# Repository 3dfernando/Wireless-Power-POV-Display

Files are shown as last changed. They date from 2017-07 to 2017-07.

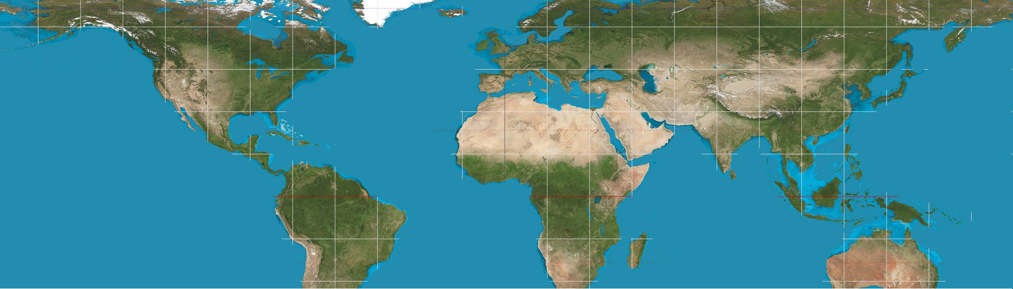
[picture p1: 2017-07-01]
04 - Images to Display/Equirectangular_projection_Cropped.jpg

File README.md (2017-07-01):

# Wireless-Power-POV-Display
This project was designed as a hobby acivity by a Mechanical Engineer. Therefore, it probably has a lot of problems from the Electrical Engineering point of view. If you think you can improve this project, please branch this Git and comment!

The project consists of a POV (Persistence of Vision) display that, unlike most of the POV displays found in the internet, is not powered by a battery but by the mains power. The regular battery-powered design is a simple solution to the problem of supplying the power needed to light up the LEDs and power the processor [Which are spinning], by making the battery also spin. 

Although the solution is effective, it's a hassle to be applied for a decorative item, for example, as one needs to stop and access the device from time to time to recharge the battery. Normally decorative objects have a no-maintenance requirement (which in some cases might be extremely difficult to achieve!).

The next easiest way of avoiding this problem is through a brushed connection. This is also possible, although it might be a little bit too noisy for a decorative device - and still would be hard for a DIY setup to require no maintenance after some hours of operation. So I thought a wireless power transfer system would be a perfect solution! So why not try it out and in the middle of the path learn more about wireless power transfer?

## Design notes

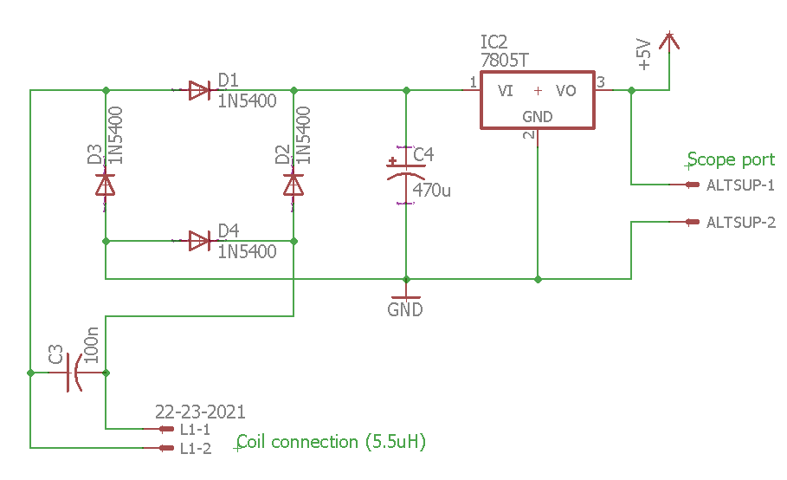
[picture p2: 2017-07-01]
02 - Electronics Design/Circuit JPGs/Power Receiver.png

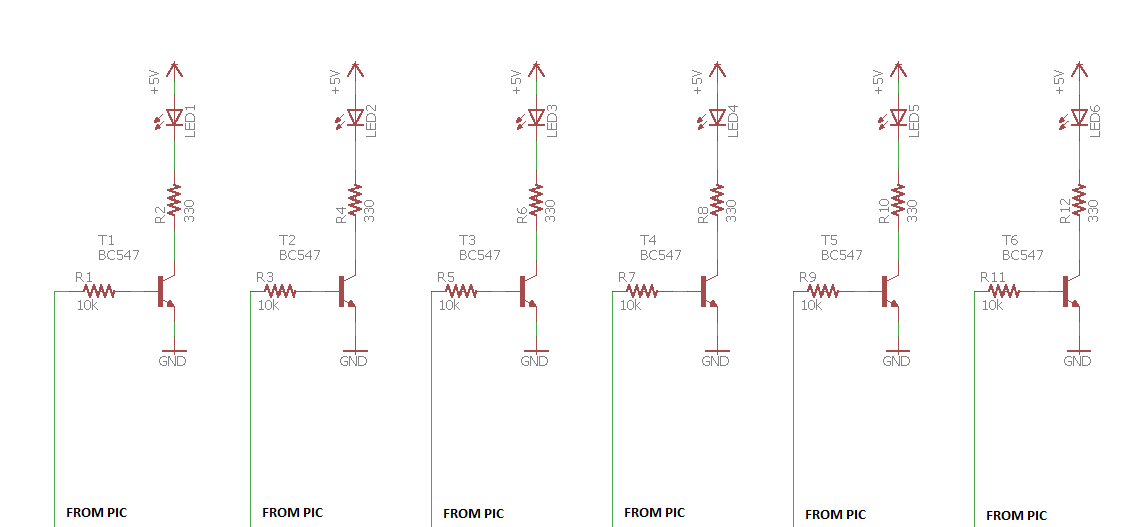
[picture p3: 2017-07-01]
02 - Electronics Design/Circuit JPGs/LED Drivers.png

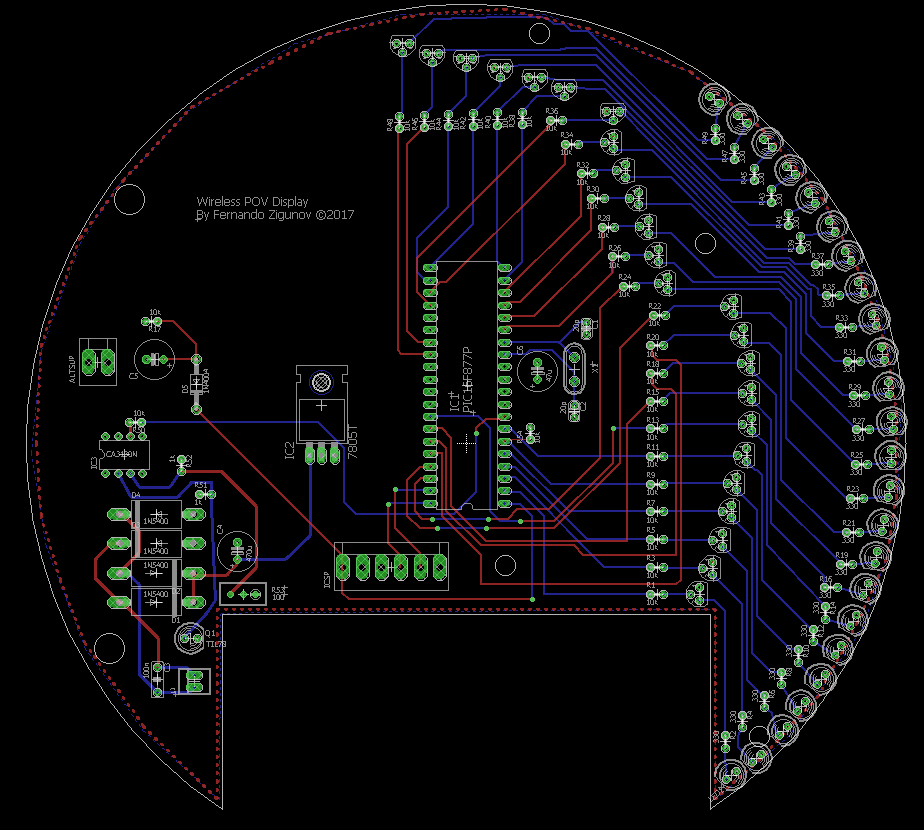
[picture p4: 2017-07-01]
02 - Electronics Design/Circuit JPGs/Receiver Board.png

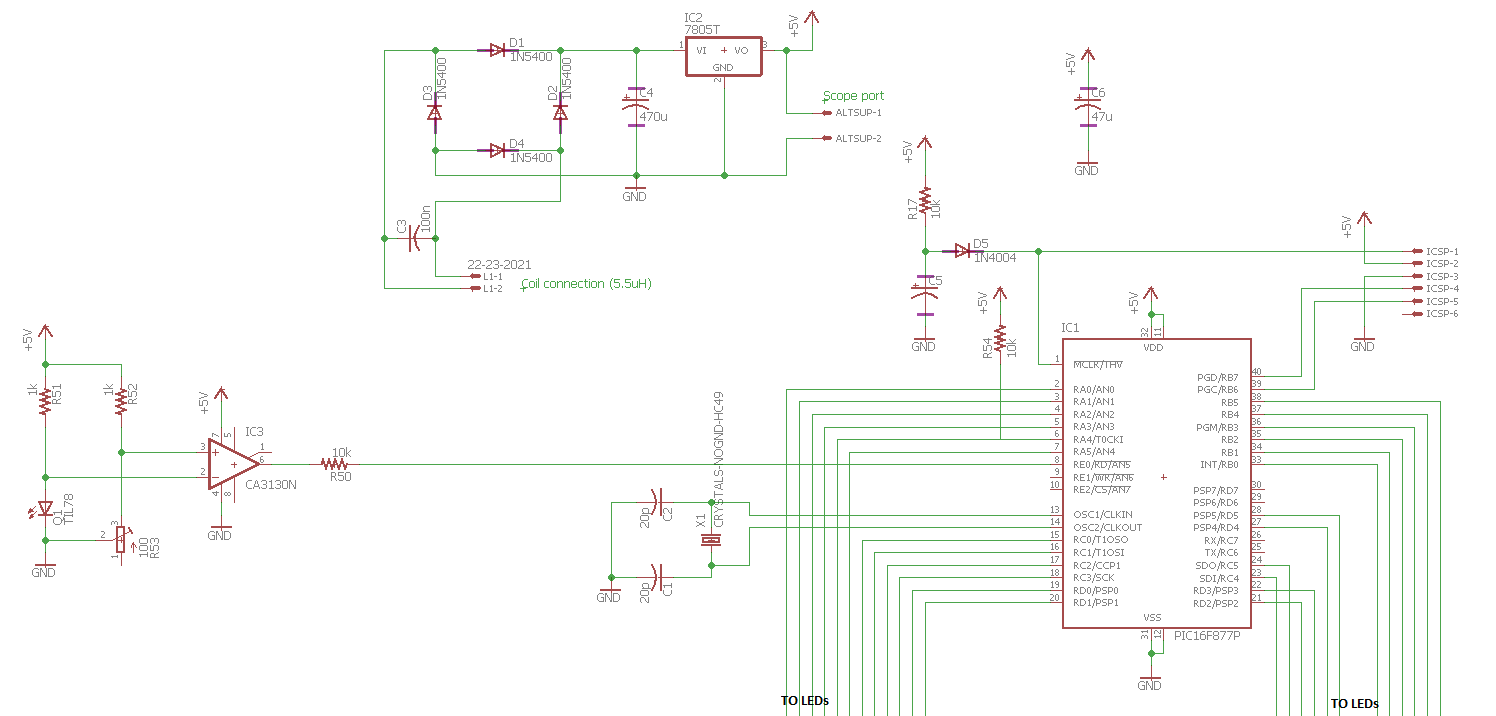
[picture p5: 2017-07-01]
02 - Electronics Design/Circuit JPGs/Power Receiver + PIC.png

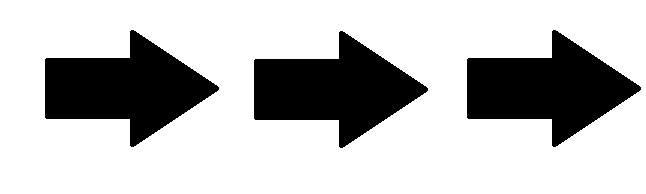
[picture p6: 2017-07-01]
04 - Images to Display/Arrows.png

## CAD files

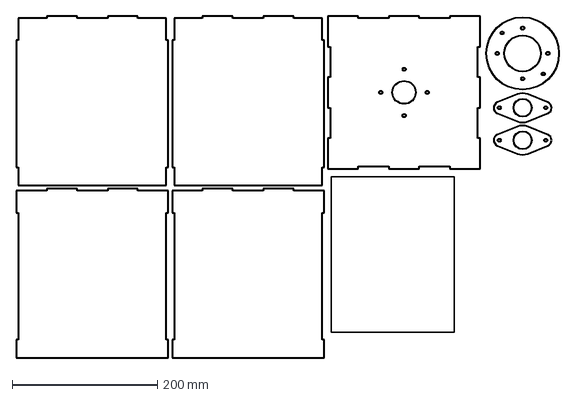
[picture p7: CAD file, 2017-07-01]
01 - Mechanical Design/Drawings/Todas Acrílico 3mm.dxf
748.5 x 471.0 mm

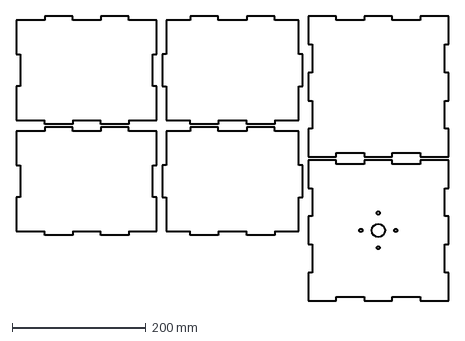
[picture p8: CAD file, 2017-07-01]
01 - Mechanical Design/Drawings/Todas MDF 6mm.dxf
646.0 x 425.0 mm

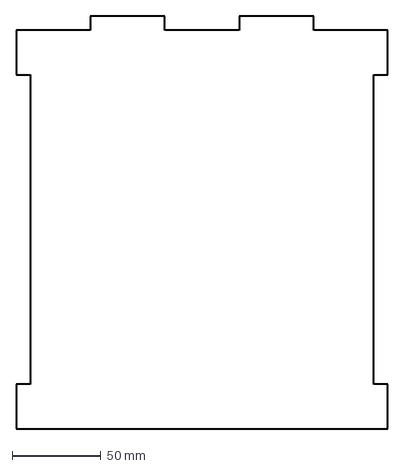
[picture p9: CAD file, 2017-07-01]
01 - Mechanical Design/Drawings/M12 - Acrílico 8mm - 2pç.dxf
210.0 x 233.0 mm

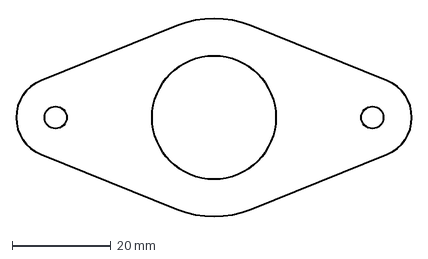
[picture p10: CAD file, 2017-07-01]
01 - Mechanical Design/Drawings/M14 - Acrílico 8mm - 2pç.dxf
80.0 x 41.0 mm

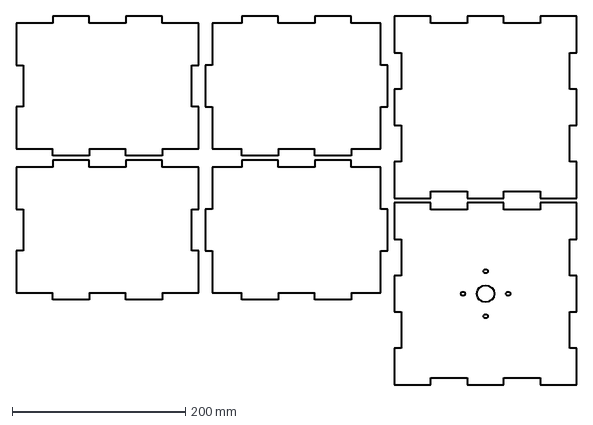
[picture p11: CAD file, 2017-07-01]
01 - Mechanical Design/Drawings/Todas MDF 8mm.dxf
646.0 x 425.0 mm

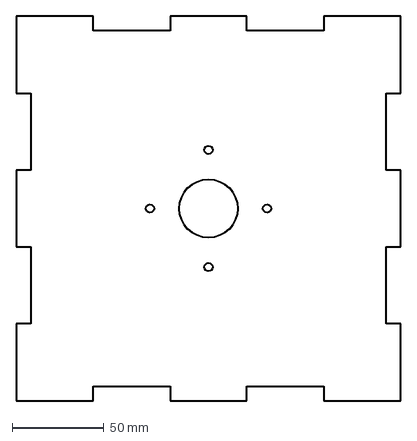
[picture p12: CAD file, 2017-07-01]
01 - Mechanical Design/Drawings/M11 - Acrílico 8mm - 1pç.dxf
210.0 x 210.0 mm

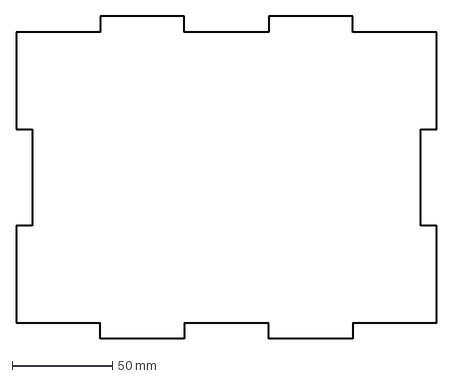
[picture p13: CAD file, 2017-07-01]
01 - Mechanical Design/Drawings/M08 - MDF 8mm - 1pç.dxf
210.0 x 161.0 mm

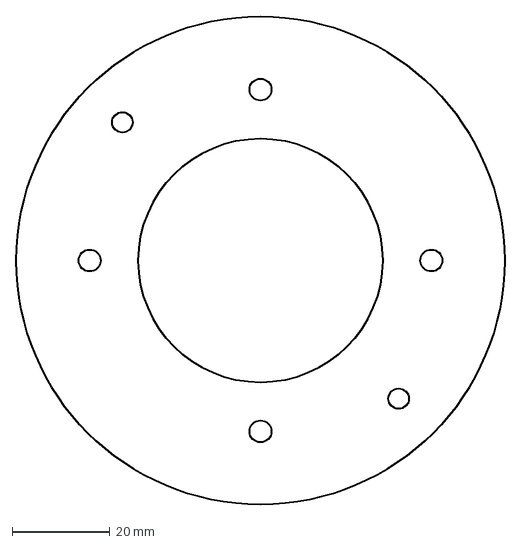
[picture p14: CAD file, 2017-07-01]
01 - Mechanical Design/Drawings/M20 - Acrílico 8mm - 1pç.dxf
100.0 x 100.0 mm

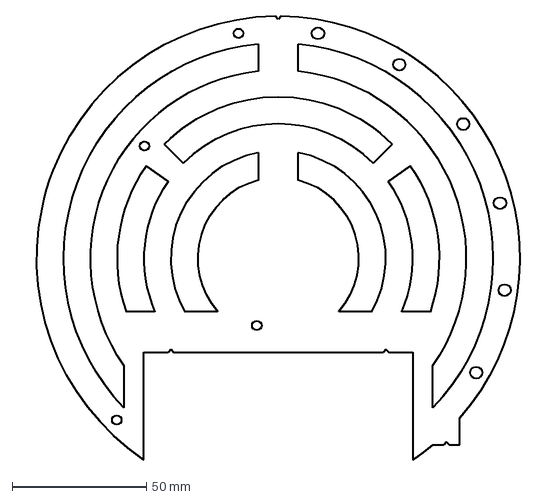
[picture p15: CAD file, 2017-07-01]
01 - Mechanical Design/Drawings/Todas Acrílico 8mm.dxf
194.0 x 164.8 mm

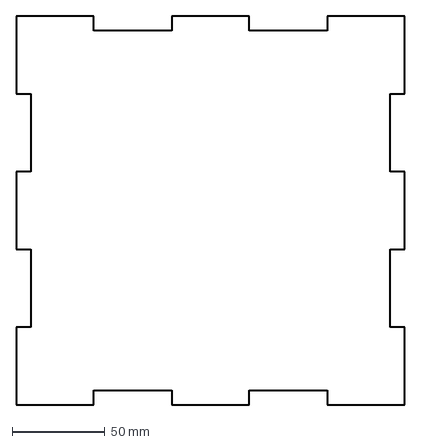
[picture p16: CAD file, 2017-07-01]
01 - Mechanical Design/Drawings/M05 - MDF 8mm - 1pç.dxf
210.0 x 210.0 mm

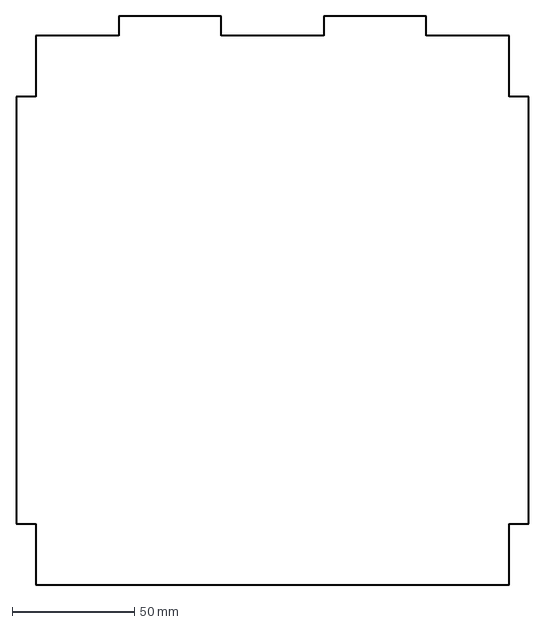
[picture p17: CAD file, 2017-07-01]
01 - Mechanical Design/Drawings/M13 - Acrílico 8mm - 2pç.dxf
210.0 x 233.0 mm

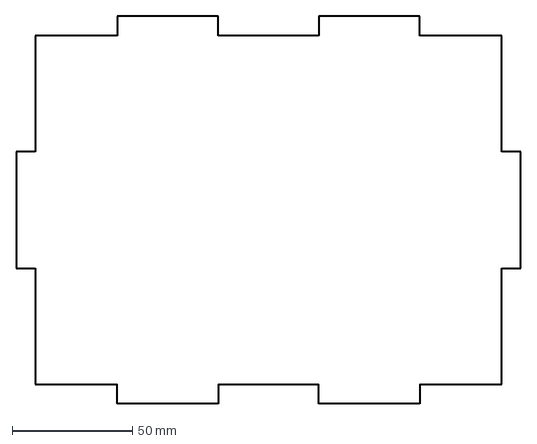
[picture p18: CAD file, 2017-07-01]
01 - Mechanical Design/Drawings/M07 - MDF 8mm - 1pç.dxf
210.0 x 161.0 mm

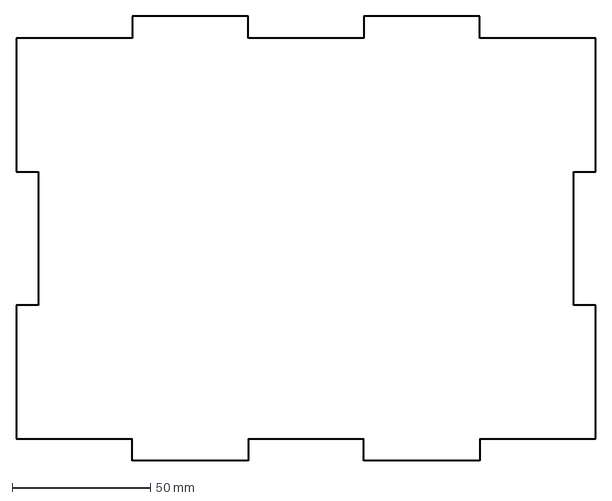
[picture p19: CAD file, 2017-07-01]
01 - Mechanical Design/Drawings/M06 - MDF 8mm - 1pç.dxf
210.0 x 161.0 mm

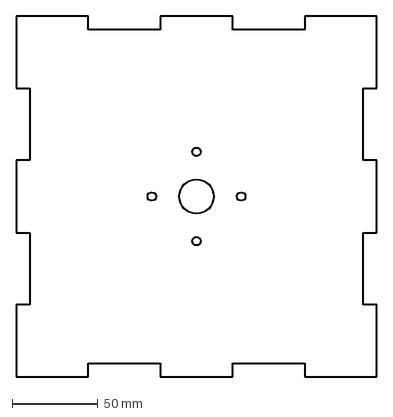
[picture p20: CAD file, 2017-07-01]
01 - Mechanical Design/Drawings/M01 - MDF 8mm - 1pç.dxf
210.0 x 210.0 mm

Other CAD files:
03 - Programming/MPLab (newer)/POVDisplay.X/dist/default/production/POVDisplay.X.production.obj
01 - Mechanical Design/Drawings/M09 - MDF 8mm - 1pç.dxf
01 - Mechanical Design/A01 - POV Display Gift Assembly.iam
01 - Mechanical Design/A02_R01 - Main Shaft Assembly.iam
01 - Mechanical Design/A03 - Base Assembly.iam
01 - Mechanical Design/A04 - Acrylic Visor.iam
01 - Mechanical Design/Drawings/M01 - Base Top.idw
01 - Mechanical Design/Drawings/M02_R01 - Main Spherical Shaft.idw
01 - Mechanical Design/Drawings/M05 - Base Bottom.idw
01 - Mechanical Design/Drawings/M06 - Wall Side 1.idw
01 - Mechanical Design/Drawings/M07 - Wall Side 2.idw
01 - Mechanical Design/Drawings/M08 - Wall Side 3.idw
01 - Mechanical Design/Drawings/M09 - Wall Side 4.idw
01 - Mechanical Design/Drawings/M11 - Acrylic Top.idw
01 - Mechanical Design/Drawings/M12 - Acrylic Side 1.idw
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

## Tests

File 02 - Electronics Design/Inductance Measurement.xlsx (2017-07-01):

Inductor Coupling Measurement
f | Voc12 | Vd12 | Voc21 | Vd21 | k
50 | 44 | 108 | 44 | 108 | 0.407
100 | 86 | 216 | 88 | 208 | 0.410
150 | 128 | 328 | 132 | 320 | 0.401
200 | 168 | 424 | 176 | 420 | 0.407
250 | 208 | 540 | 208 | 540 | 0.385
300 | 248 | 640 | 256 | 640 | 0.394
400 | 320 | 840 | 328 | 820 | 0.390
500 | 400 | 1040 | 408 | 1020 | 0.392
800 | 620 | 1560 | 620 | 1520 | 0.403
d [mm] | kavg
0 | 0.39
9 | 0.31
18 | 0.21

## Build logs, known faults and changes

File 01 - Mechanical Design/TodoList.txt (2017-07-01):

Include Hall effect sensor and magnet support in model
Model correctly the quick clamps
Include birthday etching
Design prototype board (+ purchase items)
Include switch in the wooden box
Include air vents in the wooden box

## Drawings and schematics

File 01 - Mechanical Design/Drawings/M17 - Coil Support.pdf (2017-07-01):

REV | REVISOR | DATA DESCRIÇÃO

8

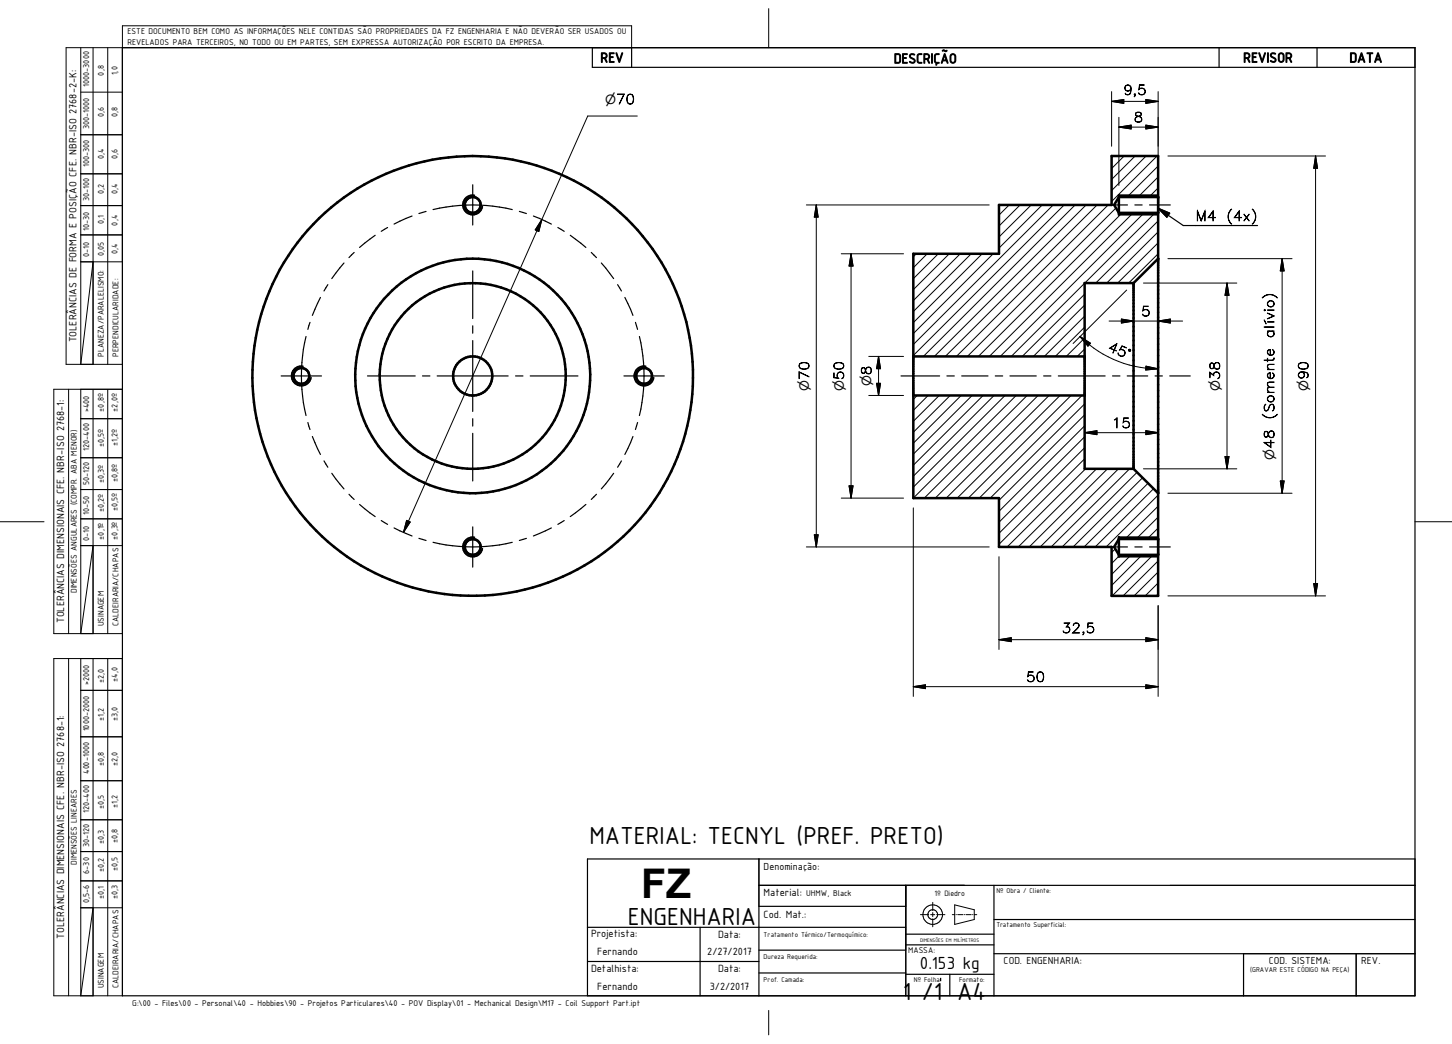
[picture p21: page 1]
Nº Obra / Cliente:; COD. SISTEMA: MASSA:; Tratamento Superficial: Projetista: Detalhista:; COD. ENGENHARIA: Nº Folha: 1 /1; Formato: A4 Material: UHMW, Black; Fernando; 3/2/2017 Data: Data:; (GRAVAR ESTE CÓDIGO NA PEÇA) FZ; n (Somente alív

ESTE DOCUMENTO BEM COMO AS INFORMAÇÕES NELE CONTIDAS SÃO PROPRIEDADES DA FZ ENGENHARIA E NÃO DEVERÃO SER USADOS OU
REVELADOS PARA TERCEIROS, NO TODO OU EM PARTES, SEM EXPRESSA AUTORIZAÇÃO POR ESCRITO DA EMPRESA.

PLANEZA/PARALEL SI MO: PERPENDICULAR DI ADE: 0 4, 0 4, 0 4, 0 6, 0,8 1,0 TOLERÂNC AI S DE FORMA E POS ÇI ÃO CFE. NBR- SI O 2768-2-K: 0-10 10-30 30-100 100-300 300-1000 1000-3000

0-10 10-50 50-120 120-400 >400 TOLERÂNC AI S DIMENS OI NA SI CFE. NBR- SI O 2768-1: ±0,1º ±0 2, º ±0 3, º ±0 5, º ±0 8, º

±0 3, º ±0,5º ±0 8, º ±1 2, º ±2 0, º D MI ENSÕES ANGULARES (COMPR. ABA MENOR) CALDEIRAR AI /CHAPAS

US NI AGEM

0 5, -6 6-30 30-¹20 ¹20-4⁰⁰ 4⁰⁰⁻¹⁰⁰⁰ ¹⁰⁰⁰⁻²⁰⁰⁰ >2000 | G:\00 - Files\00 - Personal\40 - Hobbies\90 - Projetos Particulares\40 - POV Display\01 - Mechanical Design\M17 - Coil Support Part.ipt TOLERÂNC AI S D MI ENS OI NAIS CFE. NBR⁻ISO ²⁷⁶⁸⁻¹:

±0,1 ±0 2, ±0,3 ±0,5 ±0,8 ±1,2 ±2,0 D MI ENSÕES LINEARES

CALDE RI AR AI /CHAPAS ±0,3 ±0 5, ±0 8, ±1,2 ±2,0 ±3,0 ±4,0

MATERIAL: TECNYL (PREF. PRETO)

ENGENHARIA | Denominação: 1º Diedro

Cod. Mat.: Tratamento Térmico/Termoquímico: Dureza Requerida: Prof. Camada: Fernando

REV. DIMENSÕES EM MILÍMETROS

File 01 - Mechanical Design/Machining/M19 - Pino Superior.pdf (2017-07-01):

REV | REVISOR | DATA DESCRIÇÃO

50

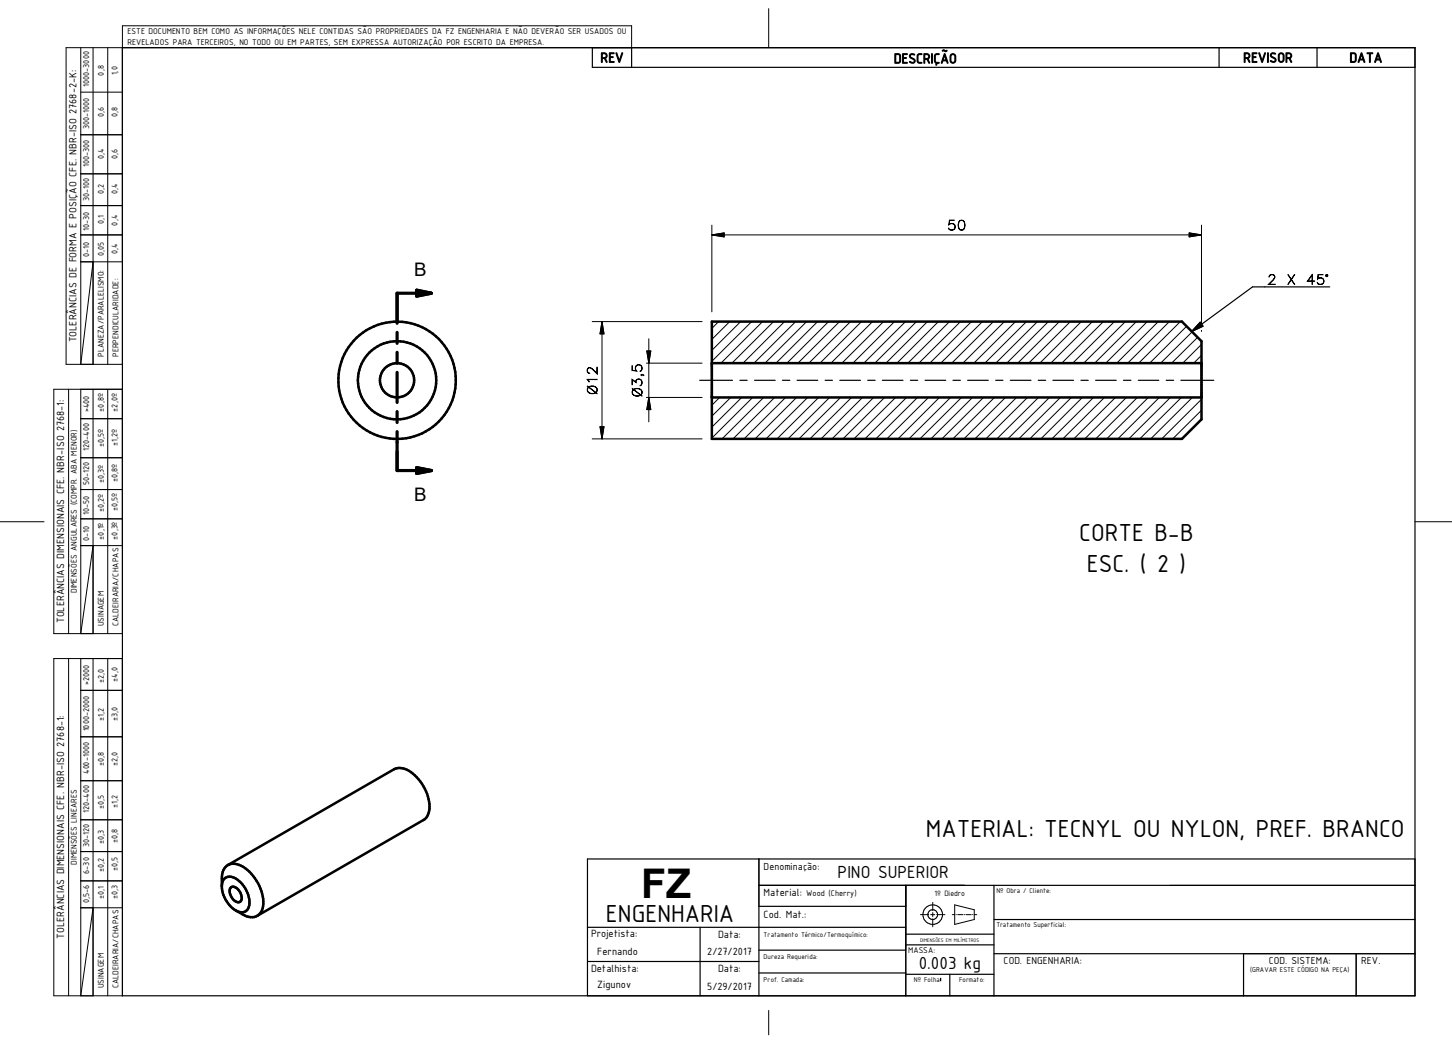
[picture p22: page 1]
CORTE B-B ESC. ( 2 ); Denominação:; 1º Diedro; Nº Obra / Cliente:; COD. SISTEMA: MASSA:; Tratamento Superficial: Projetista: Detalhista:; COD. ENGENHARIA: Nº Folha:; Formato: Material: Wood (Cherry) Cod. Mat.: Tratamento Térmico/Termoquímico: Dureza Requerida: Prof. Camada: Fernando Zigunov; 5/29/2017 Data: Data:; (GRAVAR ESTE CÓDIGO NA PEÇA) FZ; ENGENHARIA; PINO SUPERIOR

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

US NI AGEM

TOLERÂNC AI S D MI ENS OI NAIS CFE. NBR-ISO 2768-1: 0 5, -6 6-30 30-120 120-400 400-1000 1000-2000 >2000

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

MATERIAL: TECNYL OU NYLON, PREF. BRANCO

REV. DIMENSÕES EM MILÍMETROS

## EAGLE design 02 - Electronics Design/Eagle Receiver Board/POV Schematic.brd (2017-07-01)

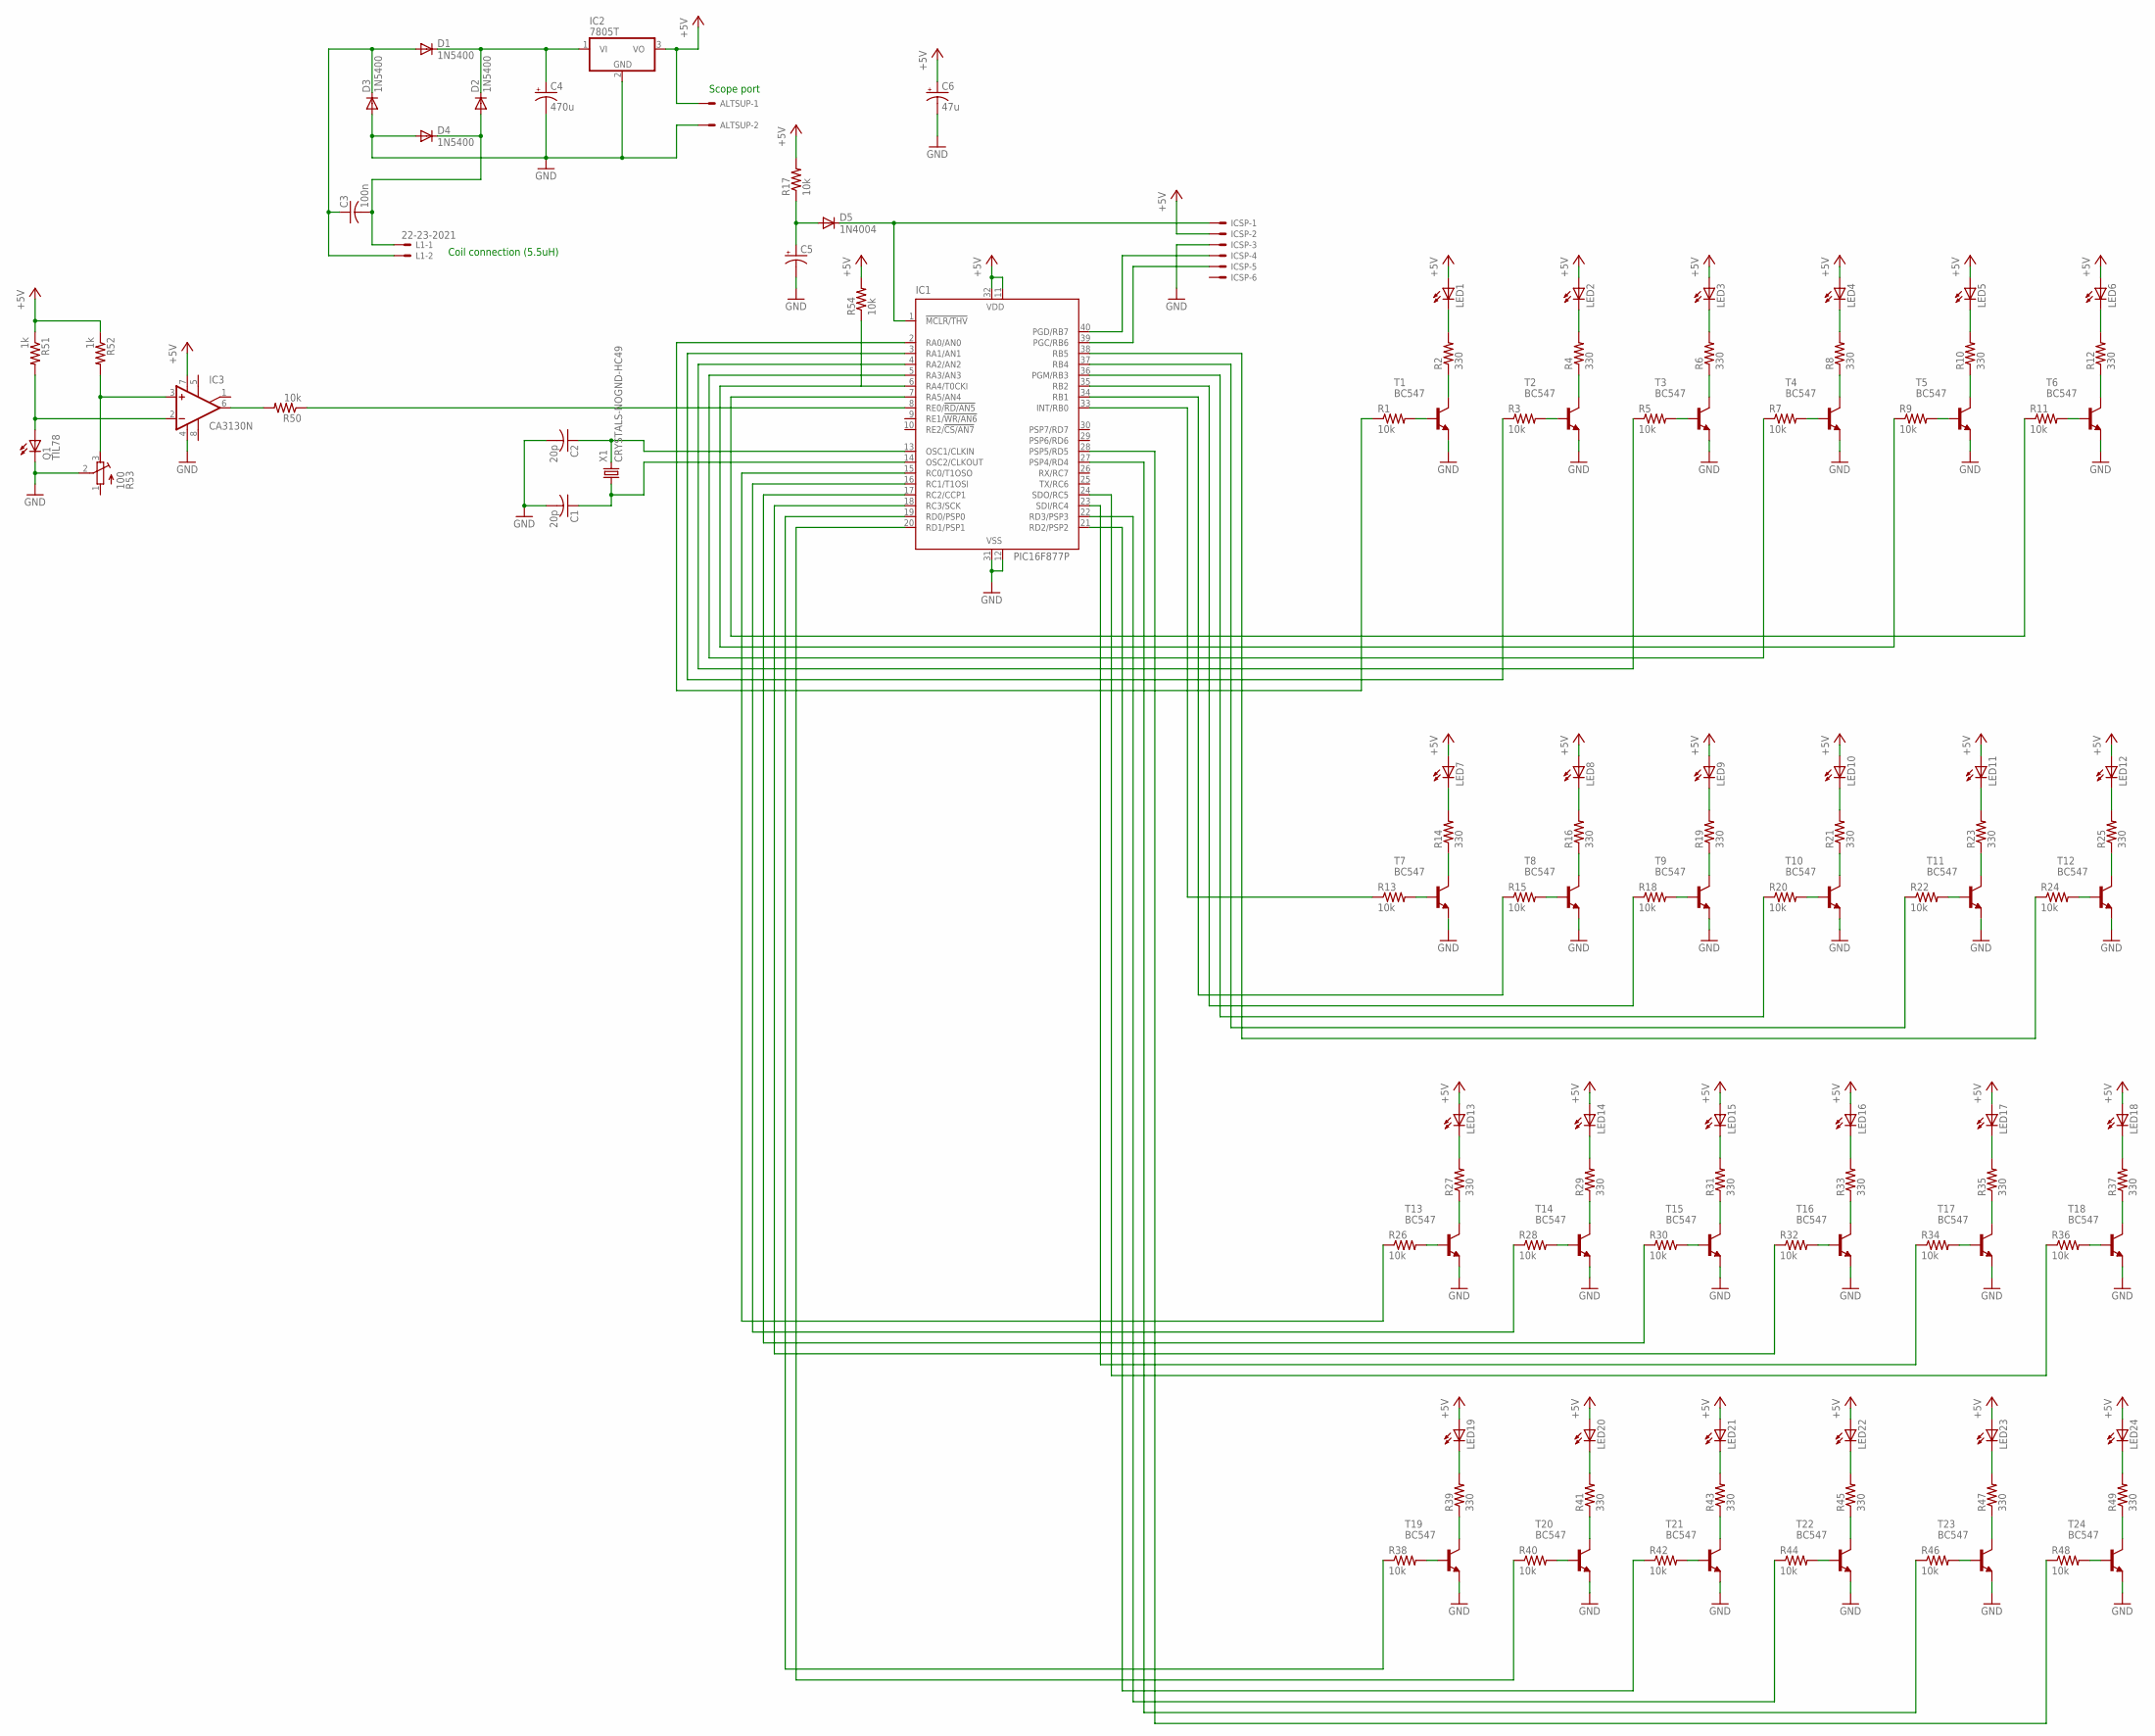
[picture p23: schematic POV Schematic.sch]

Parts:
ALTSUP: KK-156-2
C1, C2: 20p; C025-024X044
C3: 100n; C050-025X075
C4: 470u; E3,5-8
C5: CPOL-USE3.5-8; E3,5-8
C6: 47u; E3,5-8
D1, D2, D3, D4: 1N5400; DO201-15
D5: 1N4004; DO41-10
IC1: PIC16F877P; DIL40
IC2: 7805T; TO220H
IC3: CA3130N; DIL08
ICSP: KK-156-6
L1: 22-23-2021
LED1, LED2, LED3, LED4, LED5, LED6, LED7, LED8, LED9, LED10, LED11, LED12, LED13, LED14, LED15, LED16, LED17, LED18, LED19, LED20, LED21, LED22, LED23, LED24: LED5MM
Q1: TIL78; LED5MM
R1, R3, R5, R7, R9, R11, R13, R15, R17, R18, R20, R22, R24, R26, R28, R30, R32, R34, R36, R38, R40, R42, R44, R46, R48, R50, R54: 10k; 0204V
R2, R4, R6, R8, R10, R12, R14, R16, R19, R21, R23, R25, R27, R29, R31, R33, R35, R37, R39, R41, R43, R45, R47, R49: 330; 0204V
R51, R52: 1k; 0204V
R53: 100; RTRIM3296W
T1, T2, T3, T4, T5, T6, T7, T8, T9, T10, T11, T12, T13, T14, T15, T16, T17, T18, T19, T20, T21, T22, T23, T24: BC547; TO92
X1: CRYSTALS-NOGND-HC49; HC49

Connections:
+5V: ALTSUP.1, C6.+, IC1.11 (VDD), IC1.32 (VDD), IC2.3 (VO), IC3.7 (V+), ICSP.2, LED1.A, LED2.A, LED3.A, LED4.A, LED5.A, LED6.A, LED7.A, LED8.A, LED9.A, LED10.A, LED11.A, LED12.A, LED13.A, LED14.A, LED15.A, LED16.A, LED17.A, LED18.A, LED19.A, LED20.A, LED21.A, LED22.A, LED23.A, LED24.A, R17.2, R51.1, R52.1, R54.2
GND: ALTSUP.2, C1.2, C2.2, C4.-, C5.-, C6.-, D3.A, D4.A, IC1.12 (VSS), IC1.31 (VSS), IC2.2 (GND), IC3.4 (V-), ICSP.3, Q1.K (C), R53.2 (S), T1.1 (E), T2.1 (E), T3.1 (E), T4.1 (E), T5.1 (E), T6.1 (E), T7.1 (E), T8.1 (E), T9.1 (E), T10.1 (E), T11.1 (E), T12.1 (E), T13.1 (E), T14.1 (E), T15.1 (E), T16.1 (E), T17.1 (E), T18.1 (E), T19.1 (E), T20.1 (E), T21.1 (E), T22.1 (E), T23.1 (E), T24.1 (E)
unnamed: C3.2, D2.A, D4.C, L1.1
unnamed: C3.1, D1.A, D3.C, L1.2
unnamed: D5.C, IC1.1 (!MCLR/THV), ICSP.1
unnamed: C5.+, D5.A, R17.1
unnamed: C2.1, IC1.13 (OSC1/CLKIN), X1.2
unnamed: C4.+, D1.C, D2.C, IC2.1 (VI)
unnamed: C1.1, IC1.14 (OSC2/CLKOUT), X1.1
unnamed: R2.1, T1.3 (C)
unnamed: LED1.K (C), R2.2
unnamed: R1.2, T1.2 (B)
unnamed: R4.1, T2.3 (C)
unnamed: LED2.K (C), R4.2
unnamed: R3.2, T2.2 (B)
unnamed: R6.1, T3.3 (C)
unnamed: LED3.K (C), R6.2
unnamed: R5.2, T3.2 (B)
unnamed: R8.1, T4.3 (C)
unnamed: LED4.K (C), R8.2
unnamed: R7.2, T4.2 (B)
unnamed: R10.1, T5.3 (C)
unnamed: LED5.K (C), R10.2
unnamed: R9.2, T5.2 (B)
unnamed: R12.1, T6.3 (C)
unnamed: LED6.K (C), R12.2
unnamed: R11.2, T6.2 (B)
unnamed: R14.1, T7.3 (C)
unnamed: LED7.K (C), R14.2
unnamed: R13.2, T7.2 (B)
unnamed: R16.1, T8.3 (C)
unnamed: LED8.K (C), R16.2
unnamed: R15.2, T8.2 (B)
unnamed: R39.1, T19.3 (C)
unnamed: IC1.40 (PGD/RB7), ICSP.4
unnamed: IC1.39 (PGC/RB6), ICSP.5
unnamed: IC1.2 (RA0/AN0), R1.1
unnamed: IC1.3 (RA1/AN1), R3.1
unnamed: IC1.4 (RA2/AN2), R5.1
unnamed: IC1.5 (RA3/AN3), R7.1
unnamed: IC1.7 (RA5/AN4), R11.1
unnamed: R19.1, T9.3 (C)
unnamed: LED9.K (C), R19.2
unnamed: R18.2, T9.2 (B)
unnamed: R21.1, T10.3 (C)
unnamed: LED10.K (C), R21.2
unnamed: R20.2, T10.2 (B)
unnamed: R23.1, T11.3 (C)
unnamed: LED11.K (C), R23.2
unnamed: R22.2, T11.2 (B)
unnamed: R25.1, T12.3 (C)
unnamed: LED12.K (C), R25.2
unnamed: R24.2, T12.2 (B)
unnamed: IC1.33 (INT/RB0), R13.1
unnamed: IC1.34 (RB1), R15.1
unnamed: IC1.35 (RB2), R18.1
unnamed: IC1.36 (PGM/RB3), R20.1
unnamed: IC1.37 (RB4), R22.1
unnamed: IC1.38 (RB5), R24.1
unnamed: R27.1, T13.3 (C)
unnamed: LED13.K (C), R27.2
unnamed: R26.2, T13.2 (B)
unnamed: R29.1, T14.3 (C)
unnamed: LED14.K (C), R29.2
unnamed: R28.2, T14.2 (B)
unnamed: R31.1, T15.3 (C)
unnamed: LED15.K (C), R31.2
unnamed: R30.2, T15.2 (B)
unnamed: R33.1, T16.3 (C)
unnamed: LED16.K (C), R33.2
unnamed: R32.2, T16.2 (B)
unnamed: R35.1, T17.3 (C)
unnamed: LED17.K (C), R35.2
unnamed: R34.2, T17.2 (B)
unnamed: R37.1, T18.3 (C)
unnamed: LED18.K (C), R37.2
unnamed: R36.2, T18.2 (B)
unnamed: LED19.K (C), R39.2
unnamed: R38.2, T19.2 (B)
unnamed: R41.1, T20.3 (C)
unnamed: LED20.K (C), R41.2
unnamed: R40.2, T20.2 (B)
unnamed: R43.1, T21.3 (C)
unnamed: LED21.K (C), R43.2
unnamed: R42.2, T21.2 (B)
unnamed: R45.1, T22.3 (C)
unnamed: LED22.K (C), R45.2
unnamed: R44.2, T22.2 (B)
unnamed: R47.1, T23.3 (C)
unnamed: LED23.K (C), R47.2
unnamed: R46.2, T23.2 (B)
unnamed: R49.1, T24.3 (C)
unnamed: LED24.K (C), R49.2
unnamed: R48.2, T24.2 (B)
unnamed: IC1.15 (RC0/T1OSO), R26.1
unnamed: IC1.16 (RC1/T1OSI), R28.1
unnamed: IC1.17 (RC2/CCP1), R30.1
unnamed: IC1.18 (RC3/SCK), R32.1
unnamed: IC1.23 (SDI/RC4), R34.1
unnamed: IC1.24 (SDO/RC5), R36.1
unnamed: IC1.19 (RD0/PSP0), R38.1
unnamed: IC1.20 (RD1/PSP1), R40.1
unnamed: IC1.21 (RD2/PSP2), R42.1
unnamed: IC1.22 (RD3/PSP3), R44.1
unnamed: IC1.27 (PSP4/RD4), R46.1
unnamed: IC1.28 (PSP5/RD5), R48.1
unnamed: IC3.2 (-IN), Q1.A, R51.2
unnamed: IC3.6 (OUT), R50.2
unnamed: IC1.8 (RE0/!RD/AN5), R50.1
unnamed: IC3.3 (+IN), R52.2, R53.3 (E)
unnamed: IC1.6 (RA4/T0CKI), R54.1

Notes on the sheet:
Coil connection (5.5uH)
Scope port

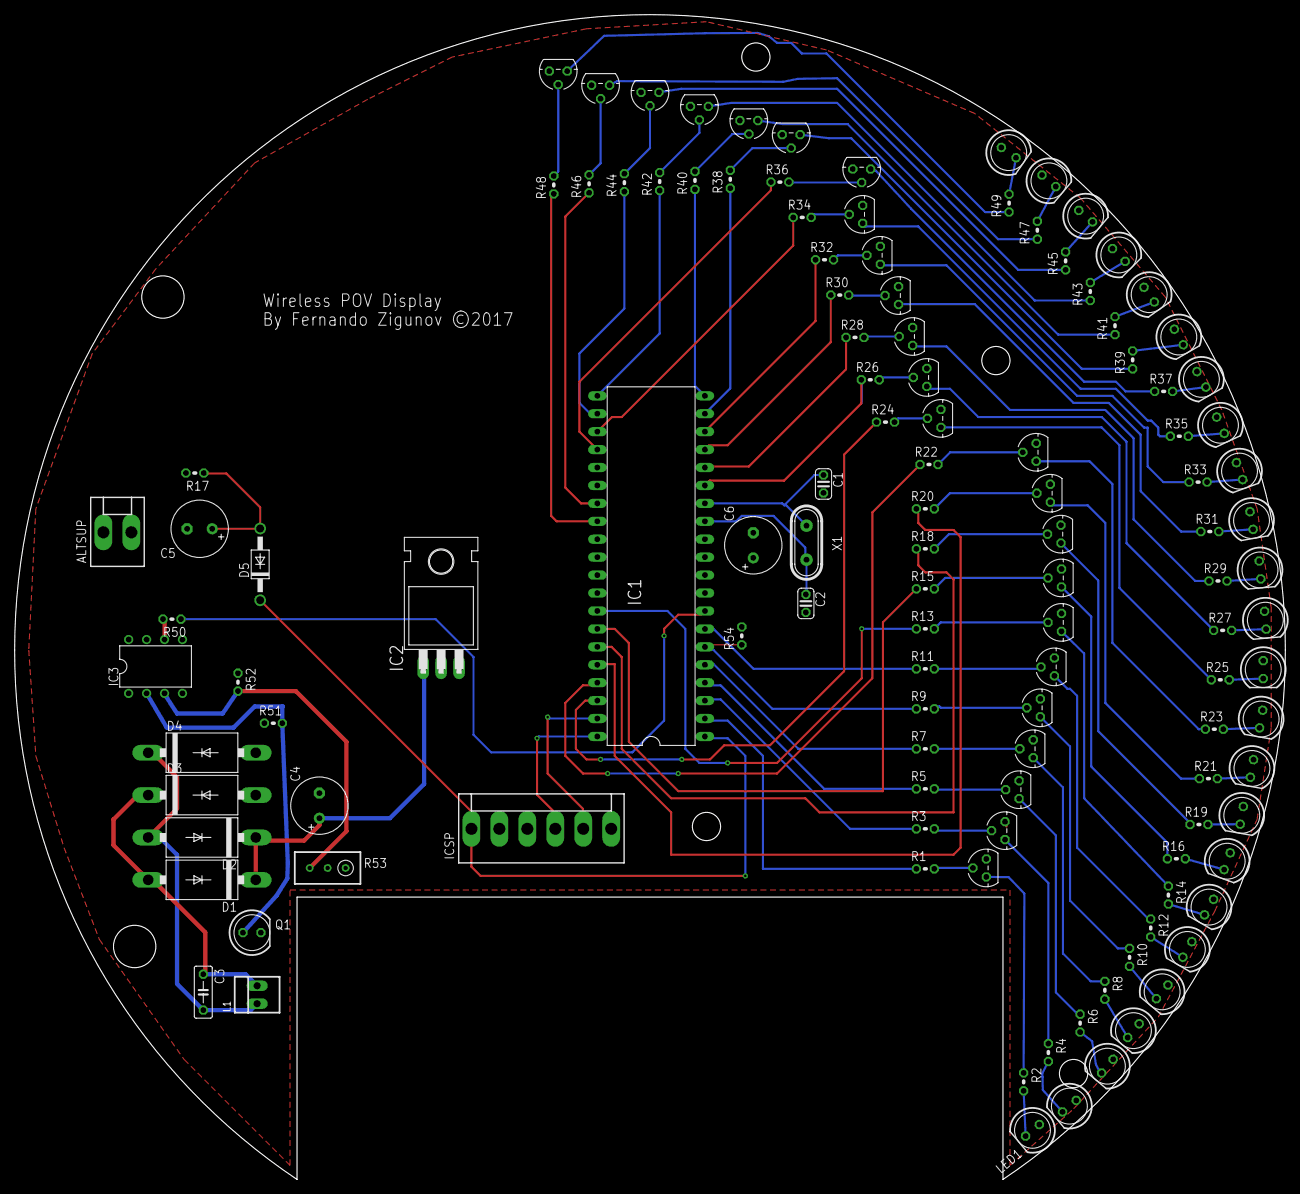
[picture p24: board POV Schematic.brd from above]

Board: 2 copper layers, 180.0 x 165.0 mm, 121 parts (0 on the bottom side), 111 nets.

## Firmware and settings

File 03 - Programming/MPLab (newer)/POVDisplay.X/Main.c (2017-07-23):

#include <xc.h>
#include "Header.h"
#include <stdio.h>
#include <stdlib.h>
#include <stdbool.h>

#define IR PORTEbits.RE0

//Constant arrays forming the images
char ImgToShow=0;
int ImageTimer=0;
int ImageTimerOverflow=30; //Ticks (of ~300ms) for the timer to overflow
const char MaxImages=4; //max images -1
//--------------------WORLD--------------------
const char WORLDD[]={0x30,0x30,0x30,0x30,0x30,0x30,0x30,0x38,0x3C,0x34,0x30,0x30,0x30,0x30,0x30,0x32,0x3A,0x3F,0x3F,0x3F,0x3F,0x3F,0x3F,0x3F,0x3F,0x3F,0x3F,0x3F,0x3F,0x3F,0x3F,0x3F,0x3F,0x3F,0x3F,0x3F,0x3F,0x3F,0x3F,0x3F,0x3F,0x3F,0x3F,0x3F,0x3F,0x3F,0x3F,0x3F,0x3F,0x3F,0x3F,0x3F,0x3F,0x3F,0x3F,0x3F,0x3F,0x3F,0x3F,0x3F,0x3F,0x3F,0x3F,0x3F,0x3F,0x3F,0x37,0x37,0x3B,0x1F,0x1F,0x1F,0x0B,0x03,0x03,0x03,0x06,0x04,0x04,0x00,0x00,0x00,0x00,0x00,0x00,0x00,0x00,0x20,0x20,0x20,0x20,0x20,0x30,0x30,0x30,0x30,0x20,0x00,0x02,0x06,0x06,0x06,0x2F,0x37,0x3F,0x2F,0x3F,0x0F,0x07,0x07,0x37,0x06,0x27,0x27,0x3F,0x3F,0x3F,0x3F,0x3F,0x3F,0x3F,0x3F,0x3F,0x3F,0x3F,0x3F,0x3F,0x3E,0x3E,0x3C,0x3C,0x38,0x38,0x38,0x30,0x30,0x30,0x30,0x30,0x38,0x38,0x38,0x38,0x30,0x30,0x00,0x00,0x00,0x00,0x20};
const char WORLDC[]={0x00,0x00,0x00,0x00,0x00,0x00,0x00,0x00,0x00,0x00,0x00,0x00,0x00,0x00,0x00,0x00,0x10,0x00,0x00,0x00,0x00,0x30,0x30,0x30,0x3C,0x3C,0x3E,0x3E,0x3E,0x3F,0x3E,0x3F,0x3F,0x3F,0x3F,0x3F,0x3E,0x3E,0x3E,0x3F,0x3F,0x3F,0x3F,0x3F,0x3F,0x3E,0x3E,0x3E,0x3E,0x3E,0x3E,0x3F,0x3F,0x1F,0x1F,0x3F,0x3F,0x3F,0x1F,0x1E,0x1F,0x17,0x17,0x37,0x27,0x27,0x27,0x07,0x07,0x0F,0x0F,0x0F,0x0F,0x0F,0x2F,0x2F,0x3F,0x3F,0x3F,0x07,0x03,0x03,0x00,0x00,0x00,0x00,0x00,0x00,0x00,0x00,0x00,0x00,0x00,0x00,0x00,0x00,0x00,0x00,0x00,0x00,0x00,0x00,0x00,0x00,0x00,0x20,0x20,0x30,0x38,0x3C,0x38,0x38,0x39,0x38,0x38,0x3C,0x3F,0x3F,0x3F,0x3E,0x3C,0x3C,0x3C,0x38,0x38,0x30,0x30,0x00,0x00,0x00,0x00,0x00,0x00,0x00,0x00,0x00,0x00,0x00,0x00,0x00,0x00,0x00,0x00,0x00,0x00,0x00,0x00,0x00,0x00,0x00};
const char WORLDB[]={0x00,0x00,0x00,0x00,0x00,0x00,0x00,0x00,0x00,0x00,0x00,0x00,0x00,0x00,0x01,0x01,0x01,0x01,0x00,0x02,0x00,0x00,0x00,0x00,0x22,0x00,0x06,0x06,0x02,0x0E,0x3C,0x33,0x26,0x34,0x20,0x00,0x00,0x00,0x00,0x00,0x00,0x28,0x30,0x30,0x00,0x00,0x00,0x00,0x00,0x00,0x00,0x00,0x00,0x20,0x38,0x2C,0x3C,0x3C,0x1E,0x3F,0x3F,0x3F,0x3F,0x3F,0x3F,0x3F,0x3F,0x3F,0x3F,0x3F,0x3E,0x3C,0x38,0x38,0x38,0x38,0x38,0x38,0x38,0x38,0x38,0x30,0x00,0x00,0x00,0x00,0x00,0x00,0x00,0x00,0x00,0x01,0x01,0x01,0x01,0x03,0x07,0x07,0x07,0x07,0x0F,0x0F,0x0F,0x0F,0x0F,0x0F,0x0F,0x0F,0x03,0x00,0x10,0x10,0x20,0x20,0x20,0x20,0x00,0x00,0x00,0x00,0x00,0x00,0x00,0x00,0x00,0x00,0x00,0x00,0x00,0x00,0x00,0x00,0x00,0x00,0x00,0x00,0x00,0x00,0x00,0x00,0x00,0x00,0x00,0x00,0x00,0x00,0x00,0x00,0x00,0x00};
const char WORLDA[]={0x00,0x00,0x00,0x00,0x00,0x00,0x00,0x00,0x00,0x00,0x00,0x07,0x03,0x07,0x0F,0x1F,0x0F,0x0F,0x1F,0x3F,0x1F,0x0F,0x0F,0x1F,0x07,0x07,0x07,0x02,0x00,0x00,0x00,0x00,0x00,0x00,0x00,0x00,0x00,0x00,0x00,0x00,0x00,0x00,0x00,0x00,0x00,0x00,0x00,0x00,0x00,0x00,0x00,0x00,0x00,0x00,0x00,0x0C,0x0C,0x00,0x10,0x30,0x38,0x3E,0x3E,0x3F,0x3F,0x3F,0x3F,0x3F,0x3E,0x38,0x00,0x00,0x00,0x00,0x00,0x00,0x00,0x00,0x00,0x00,0x00,0x00,0x00,0x00,0x00,0x00,0x00,0x00,0x00,0x00,0x20,0x30,0x38,0x3C,0x3C,0x3E,0x3F,0x3F,0x3F,0x3F,0x3F,0x3F,0x3F,0x3F,0x3F,0x30,0x30,0x20,0x00,0x00,0x00,0x00,0x00,0x00,0x00,0x00,0x00,0x00,0x00,0x00,0x00,0x00,0x00,0x00,0x00,0x00,0x00,0x00,0x00,0x00,0x00,0x00,0x00,0x00,0x00,0x00,0x00,0x00,0x00,0x00,0x00,0x00,0x00,0x00,0x00,0x00,0x00,0x00,0x00,0x00};

//--------------------ARROW--------------------
const char ARROWD[]={0x00,0x00,0x00,0x00,0x00,0x00,0x00,0x00,0x00,0x00,0x00,0x00,0x00,0x00,0x00,0x01,0x01,0x01,0x03,0x03,0x03,0x07,0x00,0x00,0x00,0x00,0x00,0x00,0x00,0x00,0x00,0x00,0x00,0x00,0x00,0x00,0x00,0x00,0x00,0x00,0x00,0x00,0x00,0x00,0x00,0x00,0x00,0x00,0x00,0x00,0x00,0x00,0x00,0x00,0x00,0x00,0x00,0x00,0x00,0x00,0x00,0x00,0x00,0x00,0x00,0x01,0x01,0x03,0x03,0x03,0x07,0x03,0x00,0x00,0x00,0x00,0x00,0x00,0x00,0x00,0x00,0x00,0x00,0x00,0x00,0x00,0x00,0x00,0x00,0x00,0x00,0x00,0x00,0x00,0x00,0x00,0x00,0x00,0x00,0x00,0x00,0x00,0x00,0x00,0x00,0x00,0x00,0x00,0x00,0x00,0x00,0x00,0x00,0x01,0x01,0x01,0x03,0x03,0x03,0x07,0x00,0x00,0x00,0x00,0x00,0x00,0x00,0x00,0x00,0x00,0x00,0x00,0x00,0x00,0x00,0x00,0x00,0x00,0x00,0x00,0x00,0x00,0x00,0x00,0x00,0x00,0x00,0x00,0x00,0x00};
const char ARROWC[]={0x00,0x03,0x03,0x03,0x07,0x07,0x0F,0x0F,0x0F,0x1F,0x1F,0x1F,0x3F,0x3F,0x3F,0x3F,0x3F,0x3F,0x3F,0x3F,0x3F,0x3F,0x1F,0x1F,0x1F,0x1F,0x1F,0x1F,0x1F,0x1F,0x1F,0x1F,0x1F,0x1F,0x1F,0x1F,0x1F,0x1F,0x1F,0x1F,0x1F,0x1F,0x00,0x00,0x00,0x00,0x00,0x00,0x00,0x00,0x00,0x03,0x03,0x07,0x07,0x07,0x0F,0x0F,0x0F,0x1F,0x1F,0x1F,0x3F,0x3F,0x3F,0x3F,0x3F,0x3F,0x3F,0x3F,0x3F,0x3F,0x1F,0x1F,0x1F,0x1F,0x1F,0x1F,0x1F,0x1F,0x1F,0x1F,0x1F,0x1F,0x1F,0x1F,0x1F,0x1F,0x1F,0x1F,0x1F,0x00,0x00,0x00,0x00,0x00,0x00,0x00,0x00,0x03,0x03,0x03,0x07,0x07,0x0F,0x0F,0x0F,0x1F,0x1F,0x1F,0x3F,0x3F,0x3F,0x3F,0x3F,0x3F,0x3F,0x3F,0x3F,0x3F,0x1F,0x1F,0x1F,0x1F,0x1F,0x1F,0x1F,0x1F,0x1F,0x1F,0x1F,0x1F,0x1F,0x1F,0x1F,0x1F,0x1F,0x1F,0x1F,0x1F,0x00,0x00,0x00,0x00,0x00,0x00,0x00,0x00,0x00,0x00};
const char ARROWB[]={0x00,0x00,0x00,0x00,0x20,0x20,0x20,0x30,0x30,0x30,0x38,0x38,0x3C,0x3C,0x3C,0x3E,0x3E,0x3E,0x3F,0x3F,0x3F,0x3F,0x38,0x38,0x38,0x38,0x38,0x38,0x38,0x38,0x38,0x38,0x38,0x38,0x38,0x38,0x38,0x38,0x38,0x38,0x38,0x38,0x00,0x00,0x00,0x00,0x00,0x00,0x00,0x00,0x00,0x00,0x00,0x20,0x20,0x20,0x30,0x30,0x30,0x38,0x38,0x3C,0x3C,0x3C,0x3E,0x3E,0x3E,0x3F,0x3F,0x3F,0x3F,0x3F,0x38,0x38,0x38,0x38,0x38,0x38,0x38,0x38,0x38,0x38,0x38,0x38,0x38,0x38,0x38,0x38,0x38,0x38,0x38,0x00,0x00,0x00,0x00,0x00,0x00,0x00,0x00,0x00,0x00,0x00,0x20,0x20,0x20,0x30,0x30,0x30,0x38,0x38,0x3C,0x3C,0x3C,0x3E,0x3E,0x3E,0x3F,0x3F,0x3F,0x3F,0x38,0x38,0x38,0x38,0x38,0x38,0x38,0x38,0x38,0x38,0x38,0x38,0x38,0x38,0x38,0x38,0x38,0x38,0x38,0x38,0x00,0x00,0x00,0x00,0x00,0x00,0x00,0x00,0x00,0x00};
const char ARROWA[]={0x00,0x00,0x00,0x00,0x00,0x00,0x00,0x00,0x00,0x00,0x00,0x00,0x00,0x00,0x00,0x00,0x00,0x00,0x00,0x00,0x00,0x20,0x00,0x00,0x00,0x00,0x00,0x00,0x00,0x00,0x00,0x00,0x00,0x00,0x00,0x00,0x00,0x00,0x00,0x00,0x00,0x00,0x00,0x00,0x00,0x00,0x00,0x00,0x00,0x00,0x00,0x00,0x00,0x00,0x00,0x00,0x00,0x00,0x00,0x00,0x00,0x00,0x00,0x00,0x00,0x00,0x00,0x00,0x00,0x00,0x20,0x00,0x00,0x00,0x00,0x00,0x00,0x00,0x00,0x00,0x00,0x00,0x00,0x00,0x00,0x00,0x00,0x00,0x00,0x00,0x00,0x00,0x00,0x00,0x00,0x00,0x00,0x00,0x00,0x00,0x00,0x00,0x00,0x00,0x00,0x00,0x00,0x00,0x00,0x00,0x00,0x00,0x00,0x00,0x00,0x00,0x00,0x00,0x00,0x20,0x00,0x00,0x00,0x00,0x00,0x00,0x00,0x00,0x00,0x00,0x00,0x00,0x00,0x00,0x00,0x00,0x00,0x00,0x00,0x00,0x00,0x00,0x00,0x00,0x00,0x00,0x00,0x00,0x00,0x00};

//--------------------SMILE--------------------
const char SMILED[]={0x00,0x00,0x00,0x00,0x00,0x00,0x00,0x00,0x01,0x07,0x07,0x0F,0x1E,0x1C,0x3C,0x39,0x39,0x39,0x39,0x39,0x39,0x3C,0x1C,0x1E,0x0F,0x07,0x07,0x01,0x00,0x00,0x00,0x00,0x00,0x00,0x00,0x00,0x00,0x00,0x00,0x00,0x00,0x00,0x00,0x00,0x00,0x00,0x00,0x01,0x07,0x07,0x0F,0x1E,0x1C,0x1C,0x38,0x38,0x38,0x38,0x38,0x38,0x1C,0x1C,0x0E,0x0F,0x07,0x03,0x01,0x00,0x00,0x00,0x00,0x00,0x00,0x00,0x00,0x00,0x00,0x00,0x00,0x00,0x00,0x00,0x00,0x00,0x01,0x07,0x07,0x0F,0x1E,0x1C,0x1C,0x38,0x38,0x38,0x38,0x38,0x38,0x1C,0x1C,0x0E,0x0F,0x07,0x03,0x01,0x00,0x00,0x00,0x00,0x00,0x00,0x00,0x00,0x00,0x00,0x00,0x00,0x00,0x00,0x00,0x00,0x00,0x01,0x07,0x07,0x0F,0x1E,0x1C,0x1C,0x38,0x38,0x38,0x38,0x38,0x38,0x1C,0x1C,0x0E,0x0F,0x07,0x03,0x01,0x00,0x00,0x00,0x00,0x00,0x00,0x00,0x00,0x00};
const char SMILEC[]={0x00,0x00,0x00,0x00,0x00,0x00,0x0F,0x3F,0x3F,0x38,0x20,0x00,0x00,0x18,0x18,0x38,0x30,0x20,0x20,0x20,0x30,0x38,0x18,0x18,0x00,0x20,0x38,0x3F,0x3F,0x0F,0x00,0x00,0x00,0x00,0x00,0x00,0x00,0x00,0x00,0x00,0x00,0x00,0x00,0x00,0x00,0x0F,0x3F,0x3F,0x38,0x20,0x00,0x00,0x1C,0x1C,0x1C,0x00,0x00,0x00,0x00,0x1C,0x1C,0x1C,0x00,0x00,0x20,0x38,0x3F,0x3F,0x0F,0x00,0x00,0x00,0x00,0x00,0x00,0x00,0x00,0x00,0x00,0x00,0x00,0x00,0x0F,0x3F,0x3F,0x38,0x20,0x00,0x00,0x1C,0x1C,0x1C,0x00,0x00,0x00,0x00,0x1C,0x1C,0x1C,0x00,0x00,0x20,0x38,0x3F,0x3F,0x0F,0x00,0x00,0x00,0x00,0x00,0x00,0x00,0x00,0x00,0x00,0x00,0x00,0x00,0x0F,0x3F,0x3F,0x38,0x20,0x00,0x00,0x1C,0x1C,0x1C,0x00,0x00,0x00,0x00,0x1C,0x1C,0x1C,0x00,0x00,0x20,0x38,0x3F,0x3F,0x0F,0x00,0x00,0x00,0x00,0x00,0x00,0x00};
const char SMILEB[]={0x00,0x00,0x00,0x00,0x00,0x00,0x38,0x3E,0x3F,0x0F,0x03,0x01,0x00,0x1C,0x1C,0x1C,0x00,0x00,0x00,0x00,0x1C,0x1C,0x1C,0x00,0x01,0x03,0x0F,0x3F,0x3E,0x38,0x00,0x00,0x00,0x00,0x00,0x00,0x00,0x00,0x00,0x00,0x00,0x00,0x00,0x00,0x00,0x38,0x3E,0x3F,0x0F,0x03,0x01,0x06,0x06,0x1E,0x1C,0x18,0x18,0x18,0x1C,0x0E,0x06,0x06,0x00,0x01,0x03,0x0F,0x3F,0x3E,0x38,0x00,0x00,0x00,0x00,0x00,0x00,0x00,0x00,0x00,0x00,0x00,0x00,0x00,0x38,0x3E,0x3F,0x0F,0x03,0x01,0x00,0x0E,0x0E,0x0E,0x0E,0x0E,0x0E,0x0E,0x0E,0x0E,0x0E,0x00,0x01,0x03,0x0F,0x3F,0x3E,0x38,0x00,0x00,0x00,0x00,0x00,0x00,0x00,0x00,0x00,0x00,0x00,0x00,0x00,0x38,0x3E,0x3F,0x0F,0x03,0x01,0x0C,0x0C,0x0E,0x07,0x03,0x03,0x03,0x07,0x0F,0x0C,0x0C,0x00,0x01,0x03,0x0F,0x3F,0x3E,0x38,0x00,0x00,0x00,0x00,0x00,0x00,0x00};
const char SMILEA[]={0x00,0x00,0x00,0x00,0x00,0x00,0x00,0x00,0x00,0x20,0x30,0x38,0x38,0x1C,0x1C,0x0E,0x0E,0x0E,0x0E,0x0E,0x0E,0x1C,0x1C,0x3C,0x38,0x30,0x30,0x00,0x00,0x00,0x00,0x00,0x00,0x00,0x00,0x00,0x00,0x00,0x00,0x00,0x00,0x00,0x00,0x00,0x00,0x00,0x00,0x00,0x30,0x30,0x38,0x3C,0x1C,0x1E,0x0E,0x0E,0x0E,0x0E,0x0E,0x0E,0x1E,0x1C,0x3C,0x38,0x30,0x30,0x00,0x00,0x00,0x00,0x00,0x00,0x00,0x00,0x00,0x00,0x00,0x00,0x00,0x00,0x00,0x00,0x00,0x00,0x00,0x30,0x30,0x38,0x3C,0x1C,0x1E,0x0E,0x0E,0x0E,0x0E,0x0E,0x0E,0x1E,0x1C,0x3C,0x38,0x30,0x30,0x00,0x00,0x00,0x00,0x00,0x00,0x00,0x00,0x00,0x00,0x00,0x00,0x00,0x00,0x00,0x00,0x00,0x00,0x00,0x30,0x30,0x38,0x3C,0x1C,0x1E,0x0E,0x0E,0x0E,0x0E,0x0E,0x0E,0x1E,0x1C,0x3C,0x38,0x30,0x30,0x00,0x00,0x00,0x00,0x00,0x00,0x00,0x00,0x00,0x00};

//--------------------CUBE--------------------
const char CUBED[]={0x00,0x00,0x00,0x00,0x00,0x00,0x00,0x00,0x00,0x00,0x00,0x00,0x00,0x00,0x00,0x00,0x00,0x00,0x00,0x00,0x00,0x00,0x00,0x00,0x00,0x00,0x00,0x00,0x00,0x00,0x00,0x00,0x00,0x00,0x00,0x00,0x00,0x00,0x00,0x00,0x00,0x00,0x00,0x00,0x00,0x00,0x00,0x00,0x00,0x00,0x00,0x00,0x00,0x00,0x00,0x00,0x00,0x00,0x00,0x00,0x00,0x00,0x00,0x00,0x00,0x00,0x00,0x00,0x00,0x00,0x00,0x00,0x00,0x00,0x00,0x00,0x00,0x00,0x00,0x00,0x00,0x00,0x00,0x00,0x00,0x00,0x00,0x00,0x01,0x03,0x07,0x0F,0x0F,0x07,0x07,0x03,0x01,0x00,0x00,0x00,0x00,0x00,0x00,0x00,0x00,0x00,0x00,0x00,0x00,0x00,0x00,0x00,0x00,0x00,0x00,0x00,0x00,0x00,0x00,0x00,0x01,0x01,0x03,0x03,0x03,0x07,0x07,0x0E,0x0E,0x1E,0x1C,0x38,0x3C,0x1C,0x1C,0x0E,0x0E,0x0F,0x07,0x07,0x03,0x03,0x01,0x01,0x01,0x00,0x00,0x00,0x00,0x00};
const char CUBEC[]={0x00,0x00,0x00,0x00,0x00,0x00,0x00,0x00,0x00,0x00,0x00,0x00,0x00,0x00,0x07,0x0F,0x1F,0x3F,0x3C,0x38,0x30,0x30,0x38,0x3E,0x3F,0x1F,0x0F,0x03,0x00,0x00,0x00,0x3F,0x3F,0x3F,0x3F,0x3F,0x00,0x00,0x00,0x3F,0x3F,0x3F,0x3F,0x3F,0x30,0x31,0x31,0x31,0x31,0x3F,0x3F,0x3F,0x3F,0x00,0x00,0x3F,0x3F,0x3F,0x3F,0x01,0x01,0x01,0x3F,0x3F,0x3F,0x3F,0x00,0x00,0x00,0x00,0x00,0x00,0x00,0x00,0x00,0x00,0x00,0x00,0x00,0x00,0x00,0x01,0x03,0x07,0x0F,0x0E,0x1E,0x3C,0x38,0x30,0x20,0x38,0x3F,0x3F,0x37,0x38,0x3C,0x3E,0x1F,0x0F,0x07,0x03,0x01,0x00,0x00,0x00,0x00,0x00,0x00,0x00,0x00,0x00,0x00,0x00,0x00,0x00,0x00,0x00,0x00,0x00,0x3F,0x3F,0x3F,0x38,0x38,0x3C,0x1C,0x1E,0x0E,0x0F,0x07,0x07,0x03,0x03,0x01,0x01,0x03,0x03,0x03,0x27,0x27,0x27,0x3E,0x3E,0x3F,0x3F,0x1F,0x00,0x00,0x00};
const char CUBEB[]={0x00,0x00,0x00,0x00,0x00,0x00,0x00,0x00,0x00,0x00,0x00,0x00,0x00,0x00,0x38,0x3E,0x3F,0x3F,0x07,0x03,0x01,0x01,0x03,0x0F,0x3F,0x3F,0x3E,0x39,0x01,0x01,0x01,0x3F,0x3F,0x3F,0x3F,0x3F,0x01,0x01,0x01,0x3F,0x3F,0x3F,0x3F,0x3F,0x01,0x21,0x21,0x21,0x21,0x3F,0x3F,0x3F,0x3F,0x00,0x00,0x3F,0x3F,0x3F,0x3F,0x20,0x20,0x20,0x3F,0x3F,0x3F,0x3F,0x00,0x00,0x00,0x00,0x00,0x00,0x00,0x00,0x00,0x00,0x00,0x0F,0x0F,0x1F,0x3F,0x3B,0x33,0x21,0x01,0x01,0x00,0x00,0x00,0x00,0x00,0x00,0x3E,0x3F,0x3F,0x01,0x00,0x00,0x00,0x20,0x30,0x38,0x3C,0x3E,0x1F,0x0F,0x07,0x03,0x00,0x00,0x00,0x00,0x00,0x00,0x00,0x00,0x00,0x00,0x00,0x00,0x3E,0x3E,0x3F,0x07,0x07,0x03,0x03,0x01,0x01,0x00,0x00,0x20,0x20,0x3F,0x3F,0x3F,0x20,0x20,0x20,0x00,0x00,0x01,0x01,0x03,0x3F,0x3F,0x3F,0x00,0x00,0x00};
const char CUBEA[]={0x00,0x00,0x00,0x00,0x00,0x00,0x00,0x00,0x00,0x00,0x00,0x00,0x00,0x00,0x00,0x00,0x00,0x20,0x20,0x20,0x20,0x20,0x20,0x20,0x20,0x00,0x00,0x20,0x20,0x20,0x20,0x20,0x20,0x20,0x20,0x20,0x20,0x20,0x20,0x20,0x20,0x20,0x20,0x00,0x20,0x20,0x20,0x20,0x20,0x20,0x20,0x20,0x20,0x00,0x00,0x20,0x20,0x20,0x20,0x00,0x00,0x00,0x20,0x20,0x20,0x20,0x00,0x00,0x00,0x00,0x00,0x00,0x00,0x00,0x00,0x00,0x00,0x00,0x00,0x00,0x20,0x20,0x30,0x30,0x30,0x38,0x38,0x38,0x3C,0x1C,0x1C,0x0E,0x0E,0x3E,0x3F,0x3F,0x0E,0x0E,0x1C,0x1C,0x1C,0x38,0x38,0x38,0x30,0x30,0x20,0x20,0x00,0x00,0x00,0x00,0x00,0x00,0x00,0x00,0x00,0x00,0x00,0x00,0x00,0x00,0x00,0x00,0x20,0x20,0x30,0x30,0x38,0x38,0x3C,0x1C,0x1E,0x3E,0x3E,0x3E,0x1C,0x1C,0x3C,0x38,0x38,0x30,0x30,0x30,0x20,0x20,0x20,0x00,0x00,0x00};

//--------------------GOODBYE--------------------
const char BYEBYED[]={0x00,0x00,0x00,0x00,0x00,0x00,0x00,0x00,0x00,0x00,0x00,0x00,0x00,0x00,0x00,0x00,0x00,0x00,0x00,0x00,0x00,0x00,0x00,0x00,0x00,0x00,0x00,0x00,0x00,0x00,0x00,0x00,0x00,0x00,0x00,0x00,0x00,0x00,0x00,0x00,0x00,0x00,0x00,0x00,0x00,0x00,0x00,0x00,0x00,0x00,0x00,0x00,0x00,0x00,0x00,0x00,0x00,0x00,0x00,0x00,0x00,0x00,0x00,0x00,0x00,0x00,0x00,0x00,0x00,0x00,0x00,0x00,0x00,0x00,0x00,0x00,0x00,0x00,0x00,0x00,0x00,0x00,0x00,0x00,0x00,0x00,0x00,0x00,0x00,0x00,0x00,0x00,0x00,0x00,0x00,0x00,0x00,0x00,0x00,0x00,0x00,0x00,0x00,0x00,0x00,0x00,0x00,0x00,0x00,0x00,0x00,0x00,0x00,0x00,0x00,0x00,0x00,0x00,0x00,0x00,0x00,0x00,0x00,0x00,0x00,0x00,0x00,0x00,0x00,0x00,0x00,0x00,0x00,0x00,0x00,0x00,0x00,0x00,0x00,0x00,0x00,0x00,0x00,0x00,0x00,0x00,0x00,0x00,0x00,0x00};
const char BYEBYEC[]={0x00,0x00,0x00,0x00,0x00,0x00,0x00,0x00,0x00,0x00,0x00,0x00,0x30,0x3F,0x3F,0x3F,0x00,0x00,0x00,0x00,0x30,0x3F,0x3F,0x3F,0x00,0x00,0x00,0x00,0x00,0x03,0x0F,0x1F,0x1E,0x1E,0x1F,0x0F,0x01,0x00,0x00,0x00,0x00,0x0F,0x1F,0x1F,0x19,0x10,0x10,0x1F,0x1F,0x1F,0x00,0x00,0x00,0x11,0x11,0x11,0x11,0x11,0x1F,0x1F,0x1F,0x00,0x00,0x00,0x00,0x00,0x00,0x1F,0x1F,0x1F,0x00,0x00,0x00,0x00,0x03,0x0F,0x1F,0x1E,0x1E,0x1F,0x0F,0x01,0x00,0x00,0x00,0x00,0x08,0x18,0x10,0x10,0x10,0x10,0x18,0x1C,0x0F,0x0F,0x07,0x01,0x00,0x00,0x00,0x00,0x00,0x00,0x00,0x18,0x1F,0x1F,0x0F,0x00,0x00,0x07,0x1F,0x1F,0x1F,0x1F,0x03,0x00,0x01,0x0F,0x1F,0x1F,0x18,0x00,0x00,0x00,0x00,0x00,0x1F,0x1F,0x1F,0x00,0x00,0x10,0x10,0x10,0x10,0x10,0x1F,0x1F,0x1F,0x00,0x00,0x00,0x00,0x00,0x00,0x00,0x00,0x00};
const char BYEBYEB[]={0x00,0x00,0x00,0x00,0x00,0x00,0x00,0x00,0x00,0x00,0x00,0x00,0x00,0x36,0x36,0x36,0x00,0x00,0x00,0x00,0x00,0x36,0x36,0x36,0x00,0x00,0x00,0x06,0x3E,0x3E,0x3C,0x38,0x18,0x18,0x38,0x3C,0x3E,0x3E,0x06,0x00,0x02,0x0E,0x1E,0x3E,0x38,0x20,0x20,0x3E,0x3E,0x3E,0x00,0x00,0x00,0x02,0x02,0x02,0x02,0x02,0x3E,0x3E,0x3E,0x00,0x02,0x02,0x02,0x02,0x02,0x3E,0x3E,0x3E,0x00,0x00,0x06,0x3E,0x3E,0x3C,0x38,0x18,0x18,0x38,0x3C,0x3E,0x3E,0x06,0x00,0x00,0x3C,0x3E,0x3E,0x22,0x22,0x22,0x06,0x0E,0x3C,0x3C,0x3C,0x20,0x00,0x00,0x00,0x00,0x00,0x00,0x00,0x00,0x00,0x38,0x3E,0x3E,0x3E,0x3E,0x3C,0x20,0x20,0x3C,0x3E,0x1E,0x3E,0x3E,0x38,0x00,0x00,0x00,0x02,0x02,0x02,0x02,0x3E,0x3E,0x3E,0x00,0x00,0x20,0x20,0x20,0x20,0x20,0x3E,0x3E,0x3E,0x00,0x00,0x00,0x00,0x00,0x00,0x00,0x00,0x00};
const char BYEBYEA[]={0x00,0x00,0x00,0x00,0x00,0x00,0x00,0x00,0x00,0x00,0x00,0x00,0x00,0x00,0x00,0x00,0x00,0x00,0x00,0x00,0x00,0x00,0x00,0x00,0x00,0x00,0x00,0x00,0x00,0x00,0x00,0x00,0x00,0x00,0x00,0x00,0x00,0x00,0x00,0x00,0x00,0x00,0x00,0x00,0x00,0x00,0x00,0x00,0x00,0x00,0x00,0x00,0x00,0x00,0x00,0x00,0x00,0x00,0x00,0x00,0x00,0x00,0x00,0x00,0x00,0x00,0x00,0x00,0x00,0x00,0x00,0x00,0x00,0x00,0x00,0x00,0x00,0x00,0x00,0x00,0x00,0x00,0x00,0x00,0x00,0x00,0x00,0x00,0x00,0x00,0x00,0x00,0x00,0x00,0x00,0x00,0x00,0x00,0x00,0x00,0x00,0x00,0x00,0x00,0x00,0x00,0x00,0x00,0x00,0x00,0x00,0x00,0x00,0x00,0x00,0x00,0x00,0x00,0x00,0x00,0x00,0x00,0x00,0x00,0x00,0x00,0x00,0x00,0x00,0x00,0x00,0x00,0x00,0x00,0x00,0x00,0x00,0x00,0x00,0x00,0x00,0x00,0x00,0x00,0x00,0x00,0x00,0x00,0x00,0x00};

//Variables
//Timer variables
char Prev_IR_State=0;
char Pixel_Column_Time=120;  
char Pixel_Column_Count=0;

//Timer control
const char Desired_Pixel_Column_Count=150;
char Last_Pixel_Column_Count=150;
char delta=0;   //Delta to cause rotation
char ArrayIndex=0;  //Actual array index to be retrieved

int diff;
float newTimeDelta;
float Kp=0.2;
int timeNow;


void main(void) {
    
    TRISA=0b00000000; //Outputs 0-5 (first 6 bits) are used only.
    TRISB=0b00000000;
    TRISC=0b00000000;
    TRISD=0b00000000;
    TRISE=0b00000011; //PortE is input
       
    ADCON0=0b00000000;// No analog
    ADCON1=0b00001110;// No analog
    OPTION_REG=0b00000010; //Sets the timer prescaler
    INTCON=0b10100000;
    
    PORTA=0b00000000;
    PORTB=0b00000000;
    PORTC=0b00000000;
    PORTD=0b00000000;    
    
    delta=Desired_Pixel_Column_Count-1;
    
    while (1) {     
        //control loop
      if (!(Last_Pixel_Column_Count==Desired_Pixel_Column_Count)) {
          //Needs to update the timer
          diff = Desired_Pixel_Column_Count-Last_Pixel_Column_Count;
          timeNow=255-Pixel_Column_Time;
          newTimeDelta = (double) timeNow * ((double) diff/ (double) Desired_Pixel_Column_Count);
          newTimeDelta = newTimeDelta * Kp; //That's gonna be the delta applied
             
          if (abs(newTimeDelta)>1) {
              Pixel_Column_Time += newTimeDelta;
              if  (Pixel_Column_Time > 250) {
                  Pixel_Column_Time=250 ;
              }
          }
      }
      
      for (int i=0; i<30; i++) {
          __delay_ms(10); //300ms delay
      }   
      
      ImageTimer++;
      if (ImageTimer>ImageTimerOverflow) {
          ImageTimer=0;
          
          ImgToShow++;
          if (ImgToShow > MaxImages) {
              ImgToShow=0;
          }
      }
        
    }       
    
}


void interrupt LEDColumn(void) {
    if (Prev_IR_State==0 && IR==1) {
        //Complete turn = 1 frame
        delta--; //Causes rotation by 1 pixel column
        if (delta==-1) {
            delta=Desired_Pixel_Column_Count-1;
        }
        
        Last_Pixel_Column_Count=Pixel_Column_Count; //Stores for control purposes
        Pixel_Column_Count=0; //Resets the column count
        
     }
    if (Pixel_Column_Count<Desired_Pixel_Column_Count) { //Don't overflow the array
        ArrayIndex=Pixel_Column_Count+delta;
        if (ArrayIndex>=Desired_Pixel_Column_Count) {
            //overflow, wrap around
            ArrayIndex=ArrayIndex-Desired_Pixel_Column_Count;
        }
        if (ImgToShow==0) {
            PORTA=WORLDA[ArrayIndex];
            PORTB=WORLDB[ArrayIndex];
            PORTC=WORLDC[ArrayIndex];
            PORTD=WORLDD[ArrayIndex];
        } else if(ImgToShow==1) {
            PORTA=BYEBYEA[ArrayIndex];
            PORTB=BYEBYEB[ArrayIndex];
            PORTC=BYEBYEC[ArrayIndex];
            PORTD=BYEBYED[ArrayIndex];
        } else if(ImgToShow==2) {
            PORTA=ARROWA[ArrayIndex];
            PORTB=ARROWB[ArrayIndex];
            PORTC=ARROWC[ArrayIndex];
            PORTD=ARROWD[ArrayIndex];
        } else if(ImgToShow==3) {
            PORTA=SMILEA[ArrayIndex];
            PORTB=SMILEB[ArrayIndex];
            PORTC=SMILEC[ArrayIndex];
            PORTD=SMILED[ArrayIndex];
        } else if(ImgToShow==4) {
            PORTA=CUBEA[ArrayIndex];
            PORTB=CUBEB[ArrayIndex];
            PORTC=CUBEC[ArrayIndex];
            PORTD=CUBED[ArrayIndex];
        } 
    }
    Prev_IR_State=IR; //Updates the state of the IR detector
    INTCONbits.T0IF=0; //Timer didn't overflow
    TMR0=Pixel_Column_Time;   //Sets the timer
    Pixel_Column_Count++; //Updates the pixel column count
}

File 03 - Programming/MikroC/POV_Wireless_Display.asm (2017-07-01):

_main:

;POV_Wireless_Display.c,36 :: 		void main() {
;POV_Wireless_Display.c,37 :: 		TRISA=0b00000000; //Outputs 0-5 (first 6 bits) are used only.
	CLRF       TRISA+0
;POV_Wireless_Display.c,38 :: 		TRISB=0b00000000;
	CLRF       TRISB+0
;POV_Wireless_Display.c,39 :: 		TRISC=0b00000000;
	CLRF       TRISC+0
;POV_Wireless_Display.c,40 :: 		TRISD=0b00000000;
	CLRF       TRISD+0
;POV_Wireless_Display.c,41 :: 		TRISE=0b00000011; //PortE is input
	MOVLW      3
	MOVWF      TRISE+0
;POV_Wireless_Display.c,43 :: 		ADCON0=0b00000000;// No analog
	CLRF       ADCON0+0
;POV_Wireless_Display.c,44 :: 		ADCON1=0b00001110;// No analog
	MOVLW      14
	MOVWF      ADCON1+0
;POV_Wireless_Display.c,45 :: 		OPTION_REG=0b00000010; //Sets the timer prescaler
	MOVLW      2
	MOVWF      OPTION_REG+0
;POV_Wireless_Display.c,46 :: 		INTCON=0b10100000;
	MOVLW      160
	MOVWF      INTCON+0
;POV_Wireless_Display.c,48 :: 		PORTA=0b00000000;
	CLRF       PORTA+0
;POV_Wireless_Display.c,49 :: 		PORTB=0b00000000;
	CLRF       PORTB+0
;POV_Wireless_Display.c,50 :: 		PORTC=0b00000000;
	CLRF       PORTC+0
;POV_Wireless_Display.c,51 :: 		PORTD=0b00000000;
	CLRF       PORTD+0
;POV_Wireless_Display.c,56 :: 		while (1) {
L_main0:
;POV_Wireless_Display.c,59 :: 		if (!(Last_Pixel_Column_Count==Desired_Pixel_Column_Count)) {
	MOVF       _Last_Pixel_Column_Count+0, 0
	XORLW      150
	BTFSC      STATUS+0, 2
	GOTO       L_main2
;POV_Wireless_Display.c,61 :: 		diff = Desired_Pixel_Column_Count-Last_Pixel_Column_Count;
	MOVF       _Last_Pixel_Column_Count+0, 0
	SUBLW      150
	MOVWF      FLOC__main+4
	CLRF       FLOC__main+5
	BTFSS      STATUS+0, 0
	DECF       FLOC__main+5, 1
	MOVF       FLOC__main+4, 0
	MOVWF      _diff+0
	MOVF       FLOC__main+5, 0
	MOVWF      _diff+1
;POV_Wireless_Display.c,62 :: 		timeNow=255-Pixel_Column_Time;
	MOVF       _Pixel_Column_Time+0, 0
	SUBLW      255
	MOVWF      R0+0
	CLRF       R0+1
	BTFSS      STATUS+0, 0
	DECF       R0+1, 1
	MOVF       R0+0, 0
	MOVWF      _timeNow+0
	MOVF       R0+1, 0
	MOVWF      _timeNow+1
;POV_Wireless_Display.c,63 :: 		newTimeDelta = (double) timeNow * ((double) diff/ (double) Desired_Pixel_Column_Count);
	CALL       _int2double+0
	MOVF       R0+0, 0
	MOVWF      FLOC__main+0
	MOVF       R0+1, 0
	MOVWF      FLOC__main+1
	MOVF       R0+2, 0
	MOVWF      FLOC__main+2
	MOVF       R0+3, 0
	MOVWF      FLOC__main+3
	MOVF       FLOC__main+4, 0
	MOVWF      R0+0
	MOVF       FLOC__main+5, 0
	MOVWF      R0+1
	CALL       _int2double+0
	MOVLW      0
	MOVWF      R4+0
	MOVLW      0
	MOVWF      R4+1
	MOVLW      22
	MOVWF      R4+2
	MOVLW      134
	MOVWF      R4+3
	CALL       _Div_32x32_FP+0
	MOVF       FLOC__main+0, 0
	MOVWF      R4+0
	MOVF       FLOC__main+1, 0
	MOVWF      R4+1
	MOVF       FLOC__main+2, 0
	MOVWF      R4+2
	MOVF       FLOC__main+3, 0
	MOVWF      R4+3
	CALL       _Mul_32x32_FP+0
	MOVF       R0+0, 0
	MOVWF      _newTimeDelta+0
	MOVF       R0+1, 0
	MOVWF      _newTimeDelta+1
	MOVF       R0+2, 0
	MOVWF      _newTimeDelta+2
	MOVF       R0+3, 0
	MOVWF      _newTimeDelta+3
;POV_Wireless_Display.c,64 :: 		newTimeDelta = newTimeDelta * Kp; //That's gonna be the delta applied
	MOVF       _Kp+0, 0
	MOVWF      R4+0
	MOVF       _Kp+1, 0
	MOVWF      R4+1
	MOVF       _Kp+2, 0
	MOVWF      R4+2
	MOVF       _Kp+3, 0
	MOVWF      R4+3
	CALL       _Mul_32x32_FP+0
	MOVF       R0+0, 0
	MOVWF      _newTimeDelta+0
	MOVF       R0+1, 0
	MOVWF      _newTimeDelta+1
	MOVF       R0+2, 0
	MOVWF      _newTimeDelta+2
	MOVF       R0+3, 0
	MOVWF      _newTimeDelta+3
;POV_Wireless_Display.c,66 :: 		if (abs(newTimeDelta)>1) {
	CALL       _double2int+0
	MOVF       R0+0, 0
	MOVWF      FARG_abs_a+0
	MOVF       R0+1, 0
	MOVWF      FARG_abs_a+1
	CALL       _abs+0
	MOVLW      128
	MOVWF      R2+0
	MOVLW      128
	XORWF      R0+1, 0
	SUBWF      R2+0, 0
	BTFSS      STATUS+0, 2
	GOTO       L__main12
	MOVF       R0+0, 0
	SUBLW      1
L__main12:
	BTFSC      STATUS+0, 0
	GOTO       L_main3
;POV_Wireless_Display.c,67 :: 		Pixel_Column_Time += newTimeDelta;
	MOVF       _Pixel_Column_Time+0, 0
	MOVWF      R0+0
	CALL       _byte2double+0
	MOVF       _newTimeDelta+0, 0
	MOVWF      R4+0
	MOVF       _newTimeDelta+1, 0
	MOVWF      R4+1
	MOVF       _newTimeDelta+2, 0
	MOVWF      R4+2
	MOVF       _newTimeDelta+3, 0
	MOVWF      R4+3
	CALL       _Add_32x32_FP+0
	CALL       _double2byte+0
	MOVF       R0+0, 0
	MOVWF      _Pixel_Column_Time+0
;POV_Wireless_Display.c,68 :: 		if  (Pixel_Column_Time > 250) {
	MOVF       R0+0, 0
	SUBLW      250
	BTFSC      STATUS+0, 0
	GOTO       L_main4
;POV_Wireless_Display.c,69 :: 		Pixel_Column_Time=250 ;
	MOVLW      250
	MOVWF      _Pixel_Column_Time+0
;POV_Wireless_Display.c,70 :: 		}
L_main4:
;POV_Wireless_Display.c,71 :: 		}
L_main3:
;POV_Wireless_Display.c,72 :: 		}
L_main2:
;POV_Wireless_Display.c,73 :: 		delay_ms(300);
	MOVLW      8
	MOVWF      R11+0
	MOVLW      157
	MOVWF      R12+0
	MOVLW      5
	MOVWF      R13+0
L_main5:
	DECFSZ     R13+0, 1
	GOTO       L_main5
	DECFSZ     R12+0, 1
	GOTO       L_main5
	DECFSZ     R11+0, 1
	GOTO       L_main5
	NOP
	NOP
;POV_Wireless_Display.c,74 :: 		}
	GOTO       L_main0
;POV_Wireless_Display.c,75 :: 		}
L_end_main:
	GOTO       $+0
; end of _main

_interrupt:
	MOVWF      R15+0
	SWAPF      STATUS+0, 0
	CLRF       STATUS+0
	MOVWF      ___saveSTATUS+0
	MOVF       PCLATH+0, 0
	MOVWF      ___savePCLATH+0
	CLRF       PCLATH+0
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

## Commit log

2017-02-24 Added resonant coupling device model in Matlab
2017-02-28 Added the wireless power transfer final circuit
2017-07-01 Uploaded the mechanical design
    [A01 - POV Display Gift Assembly.0030.iam, A01 - POV Display Gift Assembly.iam, A02 - Main Shaft Assembly.iam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]
2017-07-01 Uploaded the electronics design files
    [DX.DSN, Inductance Measurement.xlsx, POV Circuit Display.sch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]
2017-07-01 Added the programming files
    [POV_Display.cfg]
2017-07-23 Used MPLab to compile the code
    >2k words available!
    [POVDisplay.X.production.obj, POV_Display.cfg]

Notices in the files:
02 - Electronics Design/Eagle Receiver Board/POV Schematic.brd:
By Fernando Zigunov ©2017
